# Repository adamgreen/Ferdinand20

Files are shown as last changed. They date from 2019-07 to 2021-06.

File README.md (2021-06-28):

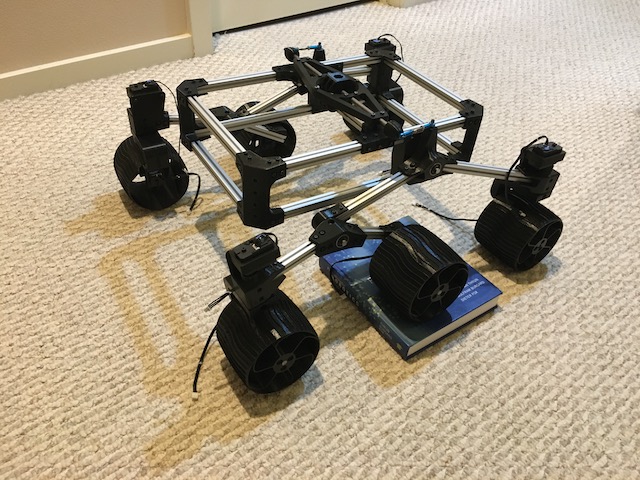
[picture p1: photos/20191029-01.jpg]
Sawppy Rover
<br>
Tracking the build of my robot to compete in the
[Seattle Robotics Society's Robo-Magellan](https://robothon.org/rules-robo-magellan/) competition that was to be held on October 3rd, 2020 at the Seattle Center but is now cancelled due to COVID-19. Development of this robot will continue in hopes that it can compete in the future.

## Points of Interest
[SRS Robo-Magellan rules](https://robothon.org/rules-robo-magellan/) <br>
[Notes about our 2014 bot](https://github.com/adamgreen/Ferdinand14#readme) <br>
[Notes from my stalled 2016 attempt](https://github.com/adamgreen/Ferdinand16#readme) <br>
[How to Clone GitHub Repository](#clone-this-repo-and-its-submodules) <br>
[Sawppy the Rover Build Instructions](https://github.com/Roger-random/Sawppy_Rover#readme) <br>

---
## June 27th, 2021
### I2C? What I2C?
The next task I set myself upon was wiring the IMU into the LPC1768 on my Sawppy bot so that I could use it with the [dead reckoning code that I wrote for the Ferdinand16 project](https://github.com/adamgreen/Ferdinand16/tree/master/firmware/robot). When I was working with the IMU hardware back in April, I had it connected to a dedicated LPC1768 on a breadboard and not the one already wired up to my bot. When I went to move it over to the LPC1768 microcontroller on the Sawppy bot, I hit a snag. All of the I2C capable pins on the microcontroller were already being used for their UART functionality: LX-16A servos/motors, MRI debug monitor, and PDB communication.

### Bridge It
In the future, I plan to create my own PCB for the LPC1768 based brains of my bot which will give me access to more pins of the microcontroller. In the meantime, I would like to continue prototyping with the mbed based board that I already have. How can I work around the lack of free I2C pins? It turns out that I still have one set of SPI pins available. Using another microcontroller, I could create a bridge device that reads the IMU sensors via I2C and then sends the resulting readings to my main microcontroller over SPI.

#### LPC1768 as SPI Slave
My first attempt at building this bridge was to use another mbed LPC1768 microcontroller as a SPI slave. When I originally skimmed the mbed SPISlave class documentation I was kind of confused on how to really use it. I then read the LPC1768 User Manual and was even more confused. I tried for several days to get the LPC1768 to reliably send data back to the SPI master but ended up throwing in the towel. I just don't think the SPI peripheral on the LPC1768 hardware is designed properly for use in slave mode:
* There is no way to get an interrupt when the master sends a single byte request. It will only interrupt when the Rx buffer overflows, the Rx FIFO is half full, or 4 byte times have elapsed since the last received byte.
* It is really hard to queue up the Tx data at the right time and if you don't have it queued in time because your code is busy doing something else, the peripheral just takes the oldest already sent data from the Tx buffer and sends it instead.

In the end, I gave up on the LPC1768 and decided to research using another microcontroller from my stash.

#### nRF5x as SPI Slave
I had an [Adafruit Feather nRF52 Pro with myNewt Bootloader - nRF52832](https://www.adafruit.com/product/3574) in my stash of development boards so I pulled up its SPI slave documentation. What I saw there looked very promising:
* You can specify what data should be returned when you have no active data queued up to be sent back.
* Once you do have data to be sent, you queue it all up at once with the help of EasyDMA.

I ported my I2C sensor reading code to the nRF52832 and quickly implemented the SPI bridging code. The SPI Slave functionality on this device worked exactly as expected and I soon had a functional bridge setup between the bot's main LPC1768 and the nRF52 bridge.

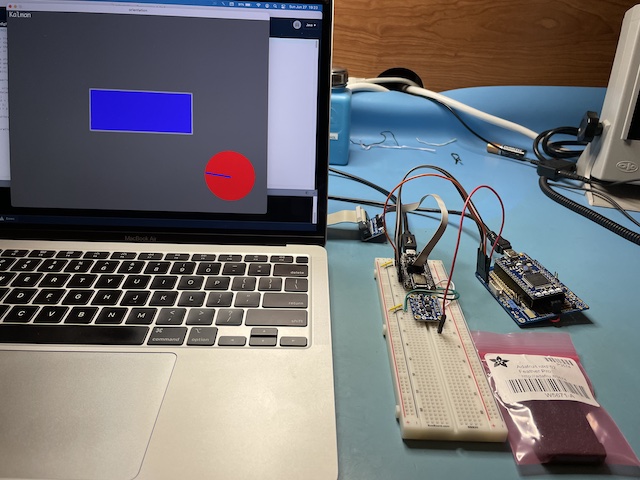
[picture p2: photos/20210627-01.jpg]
nRF52 bridge connected to LPC1768


Now to get it all installed back on my bot and start writing some dead reckoning code :)

---
## June 4th, 2021
### LX-16A Encoders
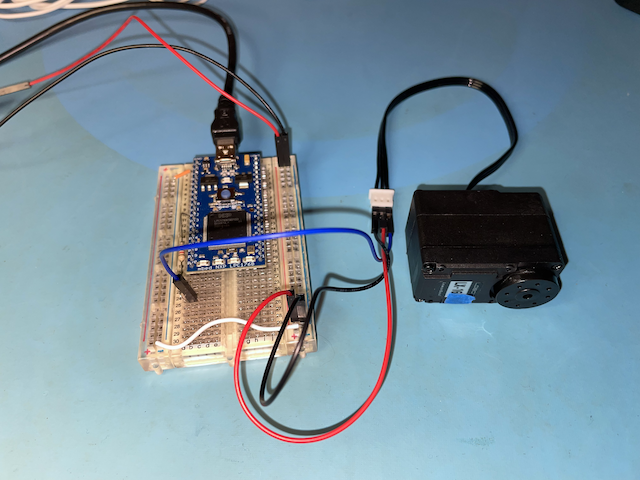
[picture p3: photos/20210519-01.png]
LX-16A Test Setup
 <br>

The [LX-16A servos](https://www.hiwonder.hk/collections/servo/products/hiwonder-lx-16a-serial-bus-servo) used in the [Sawppy Rover](https://github.com/Roger-random/Sawppy_Rover#readme) design have a potentiometer that can be used for reading out the current angle but it can't accurately read all 360 degrees of the rotation. It returns accurate readings between -40 and 280 degrees (320 degrees of rotation) but not such accurate readings for the other 40 degrees of rotation. There are 2 types of inaccurate readings that it returns when in the range between 280 and -40 degrees (the deadzone):
* It will return angle values that fall between 280 and -40 as expected but they aren't accurate. This is the most common case and is easy for me to detect in code. I suspect that there is a carbon arc for the section where it returns correct values (-40 to 280 degrees) and maybe just copper at the two extremes where it returns these incorrect readings. The following diagrams show what I think the internals of the potentiometer look like and where the wiper is located for a few key angles:
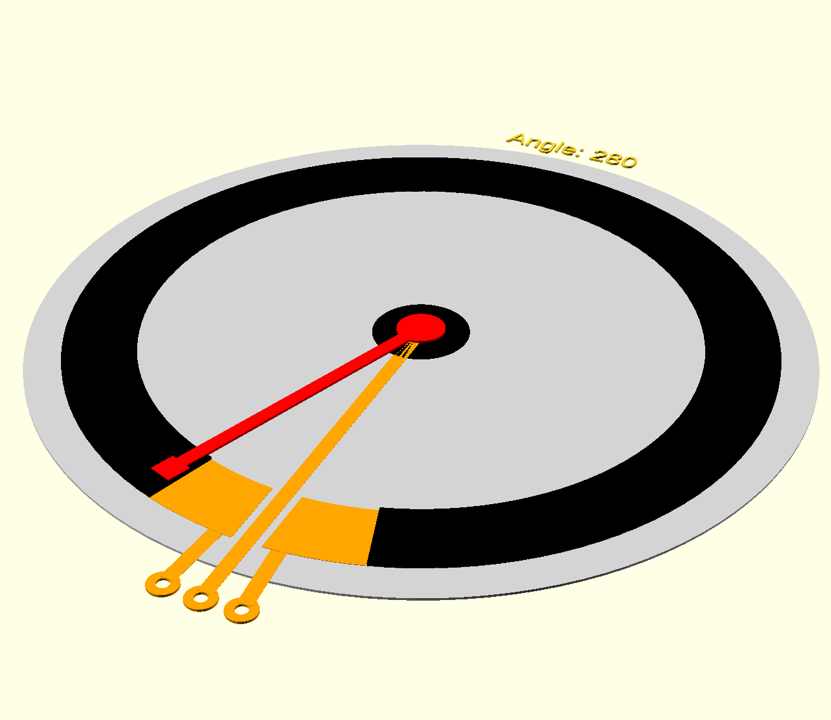
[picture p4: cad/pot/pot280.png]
Angle at 280 degrees
  * 280 degrees: This is the maximum valid angle. The potentiometer wiper is contacting the carbon resistive track. <br>
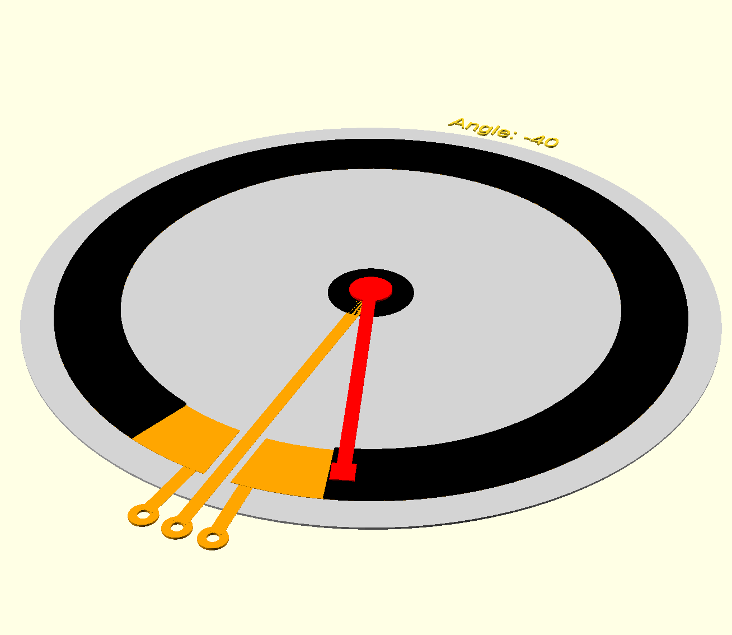
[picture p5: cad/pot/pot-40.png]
Angle at -40 degrees
  * -40 degrees: This is the minimum valid angle and shows the potentiometer wiper at the other end of the carbon resistive track. <br> 
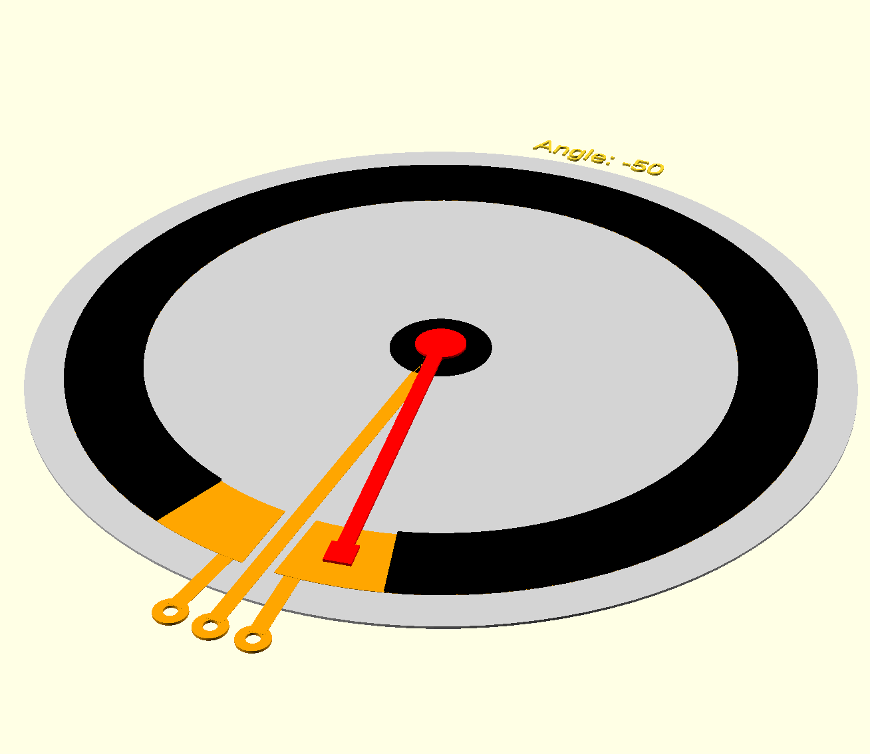
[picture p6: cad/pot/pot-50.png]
Angle at -50 degrees
  * -50 degrees: This is an angle in the deadzone. The potentiometer is no longer on the carbon resistive track but is also not floating. This explains why the readings back from the LX-16A servo tend to fall around -40 or 280 when in the deadzone since this area of the track is at either the maximum or minimum voltage level since there is so little resistance to the end taps. <br> 
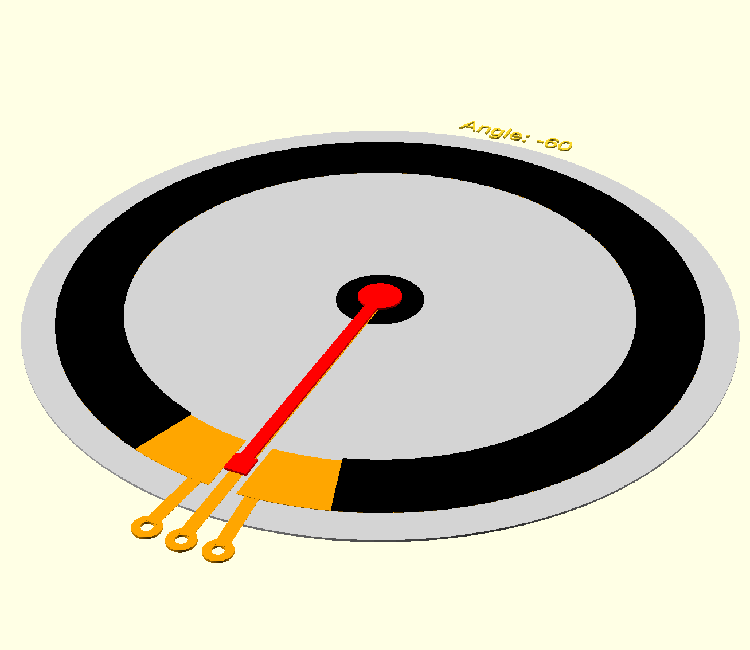
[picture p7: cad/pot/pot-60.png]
Angle at -60 degrees
* It will return random angle readings that can fall anywhere in the 360 degree range. I suspect that this happens when the potentiometer wiper is left floating in a gap that must exist between the two ends of the potentiometer to stop the wiper from creating a short between the high and low voltages applied to the opposite ends of the potentiometer. This isn't a common case and is hard to detect in code but we do know that it happens when previous readings place it in the deadzone and the wiper shouldn't dwell in this area for long at the velocities and sampling times that will be used for controlling my robot's motion. <br> 

I tried two methods to work around these inaccurate readings and I will give an overview of them below.

#### Kalman Approach
Kalman Filter Book <br>
As the old saying goes, "When all you have is a hammer, everything looks like a nail." In my case, my hammer of choice has become the Kalman filter. So my first thought to solve the LX-16A servo encoder problem was to apply a Kalman filter to calculate the current rotational position and velocity. To this end, I started out by re-reading my ["Kalman Filter for Beginners with MATLAB Examples" by Phil Kim](https://www.amazon.com/Kalman-Filter-Beginners-MATLAB-Examples/dp/1463648359). I really like this book. The content is very good. The only down point is the Korean to English translation could use quite a bit of improvement. Once I finished the reread, I wrote up some code to experiment with the Kalman filter which can be seen in the following [commit](https://github.com/adamgreen/Ferdinand20/commit/b95c3b9d9873d6a039cecfaa98e94790804dd103). I played with this code for a few days but I never got the error estimates to a point where the rotational velocity estimate wasn't overly filtered with a lagging response to real world velocity changes. Based on these results, I decided to try another approach which can be best described as a bunch of conditional hacks.

#### Conditional Hacks
The key observation that I take advantage of in my set of hacks is the following:
* If the angle returned from the LX-16A servo is between -40 and 280 degrees, then most likely it is within +/-0.24 degrees (1 lsb) of the actual real world position.

This means that my code treats such position measurements as the truth and uses them to estimate the velocity. There is one exception to this and I will discuss it more later.

The second observation is very much related to that first one:
* If the angle returned from the LX-16A servo is instead between 280 degrees and -40 degrees then it is in a deadzone where the returned values are much less accurate.

When my code detects that the returned position readings are in this deadzone, it uses the previous position and velocity estimates and sampling time to calculate new position estimates by assuming constant velocity between the samples.

The handling of those two angle ranges gets us most of the way to a solution but I needed to add a few more conditional hacks to produce a functional filter:
* When the wiper is in the middle of the deadzone, it will be floating and returning completely random values that fall in or outside of the deadzone. I have the code ignore the first non-deadzone sample when the previous sample was from the deadzone. If this ignored non-deadzone angle is followed by another then the code transitions into the non-deadzone logic previously described. This does mean that the first good angle reading is always dropped when transitioning out of the deadzone but that is a small price to pay for filtering out these completely erroneous readings. I only expect a single erroneous reading caused by a floating wiper when the rover is moving since there should be a very low likelihood that the wiper stays in this region for multiple samples as the motor is rotating.
* Don't update the velocity until it has two or more non-deadzone position readings. The last interpolated position from the deadzone logic might be so incorrect that it would result in a very bad estimate of the velocity.
* Use an exponential recursive moving average filter to smooth out the velocity calculations. We don't want high frequency noise in this calculation to later impact the PID control loop.

```c++
void LX16A_DriveMotor::updateState()
{
    // Calculate time since last running of the filter and grab the current servo position in close temporal
    // relation to the time capture.
    int16_t servoPos = m_servo.getPosition();
    uint32_t currSampleTime = m_timer.read_us();
    uint32_t elapsedMicroSec = currSampleTime - m_lastSampleTime;
    m_lastSampleTime = currSampleTime;
    float dt = (float)elapsedMicroSec / 1000000.0f;

    EncoderState prevState = m_currState;
    if (ignoringNonDeadZoneSamples(servoPos) || isServoInDeadZone(servoPos))
    {
        // The servo position could be off by as much as +/-20 degrees when in dead zone of the pot.
        // Assume that the motor is still spinning at the same rate when in dead zone.
        m_currState.angle = constrainAngle(prevState.angle + prevState.velocity * dt);
        m_currState.velocity = prevState.velocity;
        m_wasInDeadZone = true;
        printf("*");
    }
    else
    {
        // The pot reading should be accurate so use it.
        m_currState.angle = constrainAngle(servoPos * LX16A_SERVO_TO_RADIAN_VALUE);

        if (m_wasInDeadZone)
        {
            // Don't want to base current velocity off of previously interpolated position.
            m_currState.velocity = prevState.velocity;
        }
        else
        {
            // Calculate velocity from change in angle and then use weighted average so that it doesn't snap too much.
            const float weight = VELOCITY_AVERAGING_WEIGHT;
            float angleDelta = constrainAngle(fmodf(m_currState.angle - prevState.angle, 2.0f*(float)M_PI));
            float velocity = angleDelta / dt;
            m_currState.velocity = (1.0f-weight)*m_currState.velocity + weight*velocity;
        }
        m_wasInDeadZone = false;
    }

    updatePID(dt);
}
```

I may have to add code in the future to handle the motor being stopped when in the deadzone or even worse, stopped right at the point where the potentiometer wiper is left floating. I will cross this bridge once I encounter it so that I have scenarios to use for testing my attempts to resolve it.

### Closing the Loop
Once I had a way to obtain a reasonably reliable estimate of the servo's rotational velocity, I pulled over my PID code from my old [Ferdinand16 repository](https://github.com/adamgreen/Ferdinand16#readme). The biggest changes I made to this code after copying include:
* Now allowing the sample time to be changed between PID updates as the frequency of the LX-16A servo position reads may not be as consistent as my previous uses of the PID control algorithm.
* Ferdinand16 required the angle error to be normalized between +/- 180 degrees and the PID code had this hardcoded into it. I updated the code to take an optional callback for performing such normalizations when required. It isn't required for LX-16A motor velocity control.

Now that I had a way to close the loop on the control of the motor velocities, I went into the existing ```SawppyDrive``` class and plugged in my new ```LX16A_DriveMotor``` class for controlling the 6 servos that spin the wheels (while leaving the 4 turning servos as is). Once this switch had been made, I could drive my Sawppy bot around by remote control as before but now the wheel velocities were running under closed loop control.

### MRIPROG / BLEMRI Issues with new macOS and MRI Updates
When I started testing the new PID code on my actual Sawppy based robot, I hit a few issues with my Bluetooth Low Energy (BLE) programming/debugging tools that I had to address first. It turns out that it needed updates to work with the newer version of my [MRI debug monitor](https://github.com/adamgreen/mri#readme), my new MacBook Air, and Big Sur updates:
* I updated **mriprog** to move the entry point for the LPC1768 bootloader into entry.S so that I can use assembly language code to initialize the stack pointers (MSP & PSP) to the desired value since the current MRI doesn't allow for modifying the stack pointers from GDB. Once the stack pointers are set, it just branches to the original main() code.
* MRI now contains 6 more special registers in the context (MSP, PSP, PRIMASK, BASEPRI, FAULTMASK, CONTROL). I updated **mriprog**'s gdbRemote module to take these into account.
* When my new laptop communicates with the nRF51 BLE to UART bridge, it tends to corrupt a few packets that need to be resent. I made a few updates to **mriprog** to better handle these resends:
  * Instead of reporting each packet error encountered, just count them and report the number of retries at the end along with the other statistics.
  * Reduce PACKET_MAX_DATA from 16k to 4k so that if the CRC fails on a packet then less data needs to be resent.
* I updated my **blemri** code to handle a BLE change introduced with Big Sur. Once the Mac has been connected to a BLE device such as BLEMRI, Big Sur only returns the information that it cached on the first connection and this doesn't include the 128-bit service UUID from the scan response. My code used this UUID for filtering when performing BLE device discovery. I modified the firmware to no longer advertise the unique service UUID and now just advertise the Nordic UART service UUID actually supported by the device as it is no longer of use for filtering. I now have the application running on macOS perform BLE discovery with no filtering and then check the local device name on each discovered device, looking for ones named BLEMRI.
* I increased the minimum and maximum connection interval from 7.5ms to 15ms in my BLEMRI firmware to meet the Apple design recommendations. My iPhone is now able to stay connected for over 100 seconds. My iPhone would previously drop the connection when it couldn't agree with the device on connection parameters. This change doesn't decrease the throughput that much as BLE allows multiple packets to be scheduled per interval. It would increase the turn around time to get the response back from commands. The throughput is still above 5kB/s after this change so I will keep it.
* I copied the **mriprog** utility from my [older BB-8 project](https://github.com/adamgreen/bb-8/tree/master/mriprog) and placed it in its [own repository](https://github.com/adamgreen/mriprog) so that it could be included as a submodule in this Ferdinand20 repository.

### Next Steps
* ~~Debug and fix some of the issues that I encountered while performing the latest testing on my Sawppy control code.~~
* Wire the IMU into the LPC1768 on my Sawppy bot.
* Port my [heading maintaining code from my Ferdinand16 project](https://github.com/adamgreen/Ferdinand16/tree/master/firmware/robot) and get it working on this bot.

---
## April 23rd, 2021
### New IMU Hardware - Up and Running!
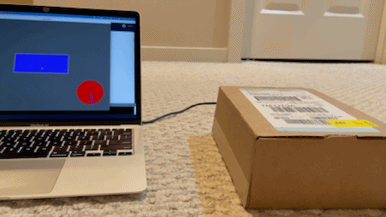
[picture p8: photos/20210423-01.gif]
Animated GIF of IMU
<br>
I spent this week getting the [Adafruit Precision NXP 9-DoF Breakout Board](https://www.adafruit.com/product/3463) working with my existing [Ferdinand16](https://github.com/adamgreen/Ferdinand16#readme) IMU code:
* I copied over the Kalman filter and I2C drivers and got them working in a newer build environment:
  * I updated my FlashFileSystem driver to work with the newer build of the mbed SDK. This file system is used to read the ```config.ini``` embedded in the firmware image as part of the build process.
  * I reorganized the code to move the drivers out into a ```libs/``` folder so that they didn't clutter up the ```software/``` folder.
* I rewrote the I2C drivers to work with the NXP FXOS8700CQ Accelerometer/Magnetometer and the NXP FXAS21002C Gyroscope:
  * My original IMU code only ran at 100Hz. I added the ability to switch between sampling rates (100/200/400Hz) from a setting in ```files/config.ini```. I am now using 200Hz for testing as 400Hz swamps the UART with too much data when communicating the orientation back to the PC in certain scenarios. It could probably run at 400Hz on the robot though as it doesn't require this communication.
  * Now samples the FXOS8700CQ Accelerometer/Magnetometer measurements on a data ready interrupt rather than a fixed timer. According to an errata from NXP, this is supposed to decrease the chance of I2C communications interfering with the magnetometer analog front end.
* I copied over my [Ferdinand14 calibration application](https://github.com/adamgreen/Ferdinand14/tree/master/calibration) and it pretty much just worked with the latest release of Processing.
* I was then able to use the calibration application to [calculate the settings for these sensors](https://github.com/adamgreen/Ferdinand14#august-19-2014) and update them in ```files/config.ini```.
* I copied over my [Ferdinand16 orientation application](https://github.com/adamgreen/Ferdinand16/tree/master/processing/orientation) and got it working on newer builds of [Processing](https://processing.org):
  * I had to use the Processing 4 alpha as the 3D graphics are broken in the current Processing 3 release on macOS.
  * I fixed some bugs that I noticed when testing my new sensor that I must have missed in previous testing 5 years ago.
  * I updated it to pull more configuration options from the ```config.ini``` rather than being hardcoded (variance settings, sampling rate, etc) in the sources. It also now reads from the same ```files/config.ini``` built into the firmware so that they use matching configuration options.
  * This program is used to measure the gyro and accelerometer/magnetometer variances to be placed in ```config.ini```. If the sensor is left unmoved for a few minutes, the statistics of how each sensor contributes to noise in the quaternion representation of the orientation will be dumped to the Processing console.

Issues I encountered while testing this port:
* The temperature readings on the NXP FXAS21002C Gyroscope  are lower resolution than the InvenSense ITG-3200 Gyroscope that I used before. This limits the resolution of the gyro drift compensation that I can use on this sensor. The good news is that this gyro shows significantly less drift during my testing at temperatures between 20 and 30C.
* While the gyro drift was pretty low when the die temperature was between 20 and 30C, it showed some very odd non-linear drift characteristics at lower temperatures which would be difficult to calibrate away. Luckily my bot isn't likely to be running at lower temperatures and the drift appears to be linear above 20C so my existing drift compensation can still be used to further reduce the drift.
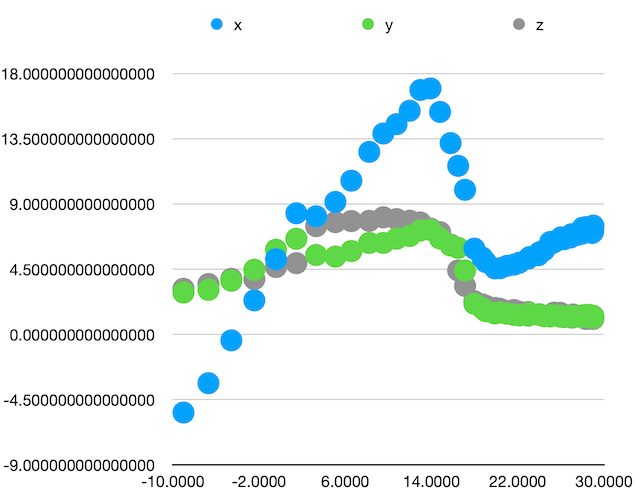
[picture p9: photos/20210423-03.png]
Drift vs Temperature Graph

* The NXP FXAS21002C Gyroscope measurements contain more noise than I encountered with the InvenSense ITG-3200 Gyroscope. The noise resulted in a 10x increase in the ```compass.gyro.variance``` setting.
```diff
-compass.initial.variance=1.0E-4
-compass.gyro.variance=6.5E-11
-compass.accelerometer.magnetometer.variance=1.0E-5
+compass.initial.variance=2.0E-4
+compass.gyro.variance=6.0E-10
+compass.accelerometer.magnetometer.variance=2.0E-4
```
* I see a lot more jitter in the orientation when run in Accelerometer/Magnetometer only mode. This jitter can also be seen in the Kalman filtered results, though much reduced as one would expect. If I hardcode the magnetometer reading and only use the accelerometer, there is almost no jitter at all so it is the magnetometer that causes it. Actually I think the accelerometer in the NXP FXOS8700CQ is better than the one I used previously.

### What's Inside the Box?
What's inside the brown box shown in the animated GIF at the beginning of this post?
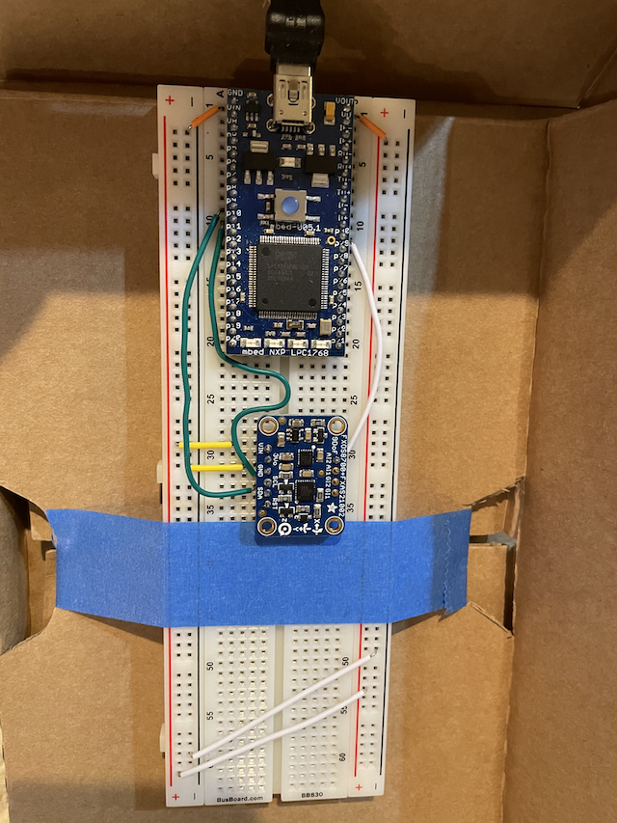
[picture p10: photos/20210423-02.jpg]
Inside the Box
<br><br>
It contains a [mbed 1768](https://os.mbed.com/platforms/mbed-LPC1768/) connected to a [Adafruit Precision NXP 9-DOF Breakout Board](https://www.adafruit.com/product/3463).

### Next Steps
Now that I have my IMU code working again on newer hardware, I want to continue fleshing out the dead reckoning part of the project. With that in mind, I will concentrate on the following next week:
* ~~Determine distance travelled by the wheels on my [Sawppy](https://github.com/Roger-random/Sawppy_Rover#readme) frame.~~

---
## April 16th, 2021
### Upgrade my IMU Hardware?
#### Sparkfun 9 DoF - Sensor Stick
Sparkfun 9 DoF - Sensor Stick</br>
Back in 2014, I decided to use the [Sparkfun 9 DoF - Sensor Stick](https://www.sparkfun.com/products/retired/10724) as the accelerometer, magnetometer, and gyroscope for our [Ferdinand14 project](https://github.com/adamgreen/Ferdinand14#readme).

#### Adafruit Precision NXP 9-DOF Breakout Board
Adafruit Precision NXP 9-DOF Breakout Board</br>
When starting out on Ferdinand20, I noticed that Sparkfun no longer sells this board. This was a good reason to look around at new sensors as I suspected there would now be even more precise units on the market. This research led me to the [Adafruit Precision NXP 9-DOF Breakout Board](https://www.adafruit.com/product/3463) which appears to offer more precision in all axis. I ordered one of these new IMU boards from Adafruit back in July of 2019. This way I would have it if I decided to make the leap and update my Kalman filter to work with a more current sensor package. I spent time this week evaluating whether I should make that leap:
* I code reviewed my existing [Kalman filter and I2C drivers](https://github.com/adamgreen/Ferdinand16/tree/master/libs/Sparkfun9DoFSensorStick). From looking at this code, it seems that the only work that would need to be completed to make the switch would be updating the I2C drivers to work with the newer NXP sensors, run a calibration pass, and update the config.ini with the new calibration data. Nothing else was specific to the sensors in use.
* I read the datasheets for the NXP FXOS8700CQ Accelerometer/Magnetometer and the NXP FXAS21002C Gyroscope to learn how difficult it would be to update the I2C drivers. From what I read in those datasheets, it should only take a part of a day to make those updates. They are pretty simple and the FXOS8700CQ datasheet even includes sample C code. I also noticed that these sensors look like they all have more precision than my current IMU hardware and can run at a higher sample rate (400Hz vs 100Hz). The only thing less precise is the temperature readings on the gyroscope which might have an impact on my drift corrections.

### Next Steps
Based on my recent research, I think it should only take a week or two to switch to this new IMU hardware:
* ~~I need to update the I2C drivers for the two chips on this new breakout board.~~
* ~~Run the resulting raw sensor readings through my [existing calibration process](https://github.com/adamgreen/Ferdinand14#august-19-2014) to create an updated config.ini.~~
* ~~Test the new hardware with my [existing Processing based GUI](https://github.com/adamgreen/Ferdinand16/tree/master/processing/orientation).~~

---
## April 11th, 2021
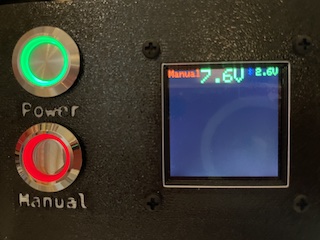
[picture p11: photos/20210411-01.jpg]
New Manual Switch


Last year I updated the Power Distribution Board enclosure to use a round push button switch for the Manual/Auto mode selection but I only had a green version of the switch on hand. I now have a [red version of the switch](https://www.adafruit.com/product/916) that I could install instead.

---
## April 9th, 2021
### BLE Remote Experiments
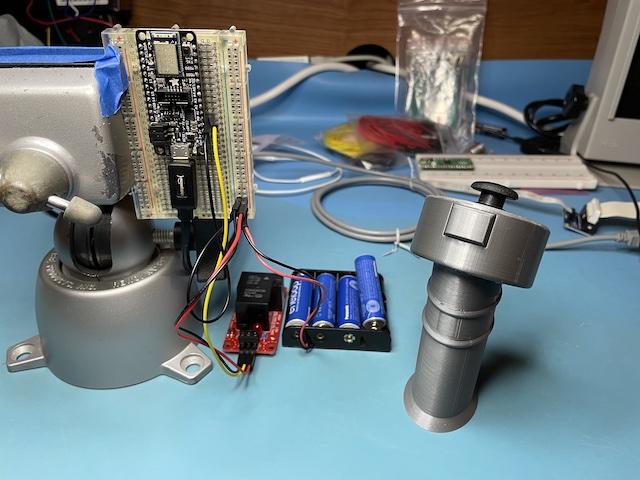
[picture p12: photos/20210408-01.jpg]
BLE Experiment


The BLE connection between the power distribution board (PDB) and the remote control that I built last year isn't as reliable as my initial prototypes. I conducted a few experiments this week to help narrow down what might be the cause. These experiments included:
* Running my PDB code on a micro:bit again like I did in the initial prototype. This did seem to work a bit better than the PDB hardware in my actual robot but not significantly better. I think the fact that I didn't initially have the logic to shutoff the relay after missing ```MAX_MISSED_BLE_PACKETS``` packets from the remote is the main reason I didn't see the problem on the earlier prototype.
* I tried moving the relay in relation to the BLE antenna. It didn't seem to have a noticeable impact. I could even place the relay right over the antenna and it didn't become any less reliable.
* If I placed a low resistance load across the relay outputs to allow a largish current (~5A) to flow, that seemed to cause more problems for the BLE connection. Especially if placed too close to the antenna.
* I tried switching to an [Adafruit Feather nRF52 Bluefruit LE - nRF52832](https://www.adafruit.com/product/3406) with its chip antenna. It actually performed worse than the micro:bit setup with its PCB antenna.
* I found that holding the remote control so that its PCB was in the vertical orientation resulted in some of the best increases in reliability, even with the PDB mounted in the actual robot.

### Lessons Learned:
* Keep high current traces on PDB away from the BLE antenna.
* Have antenna on BLE modules protruding out over the PCB if possible.
* Mount BLE PCB antenna in vertical orientation.
* For PDB, place it at top so there isn't much between it and the remote control.
* For remote, try to place it so that my hand won't be between the two antenna.

---
## March 29th, 2021
### Cone Detection?
The computer vision unit of the [RoboGrok course](http://www.robogrok.com) showed a way to highlight red objects by subtracting the green and blue channel values from the red channel value so that only pixels with red and no blue and/or green component would show up brighter. The following two screen captures show what a traffic cone and a Robothon 2015 t-shirt look like when viewed with this red-only pixel filter applied. The left window in each screen capture shows the full RGB of the scene and the right window shows the same scene with the red-only filter applied.
#### Normal Indoor Lighting
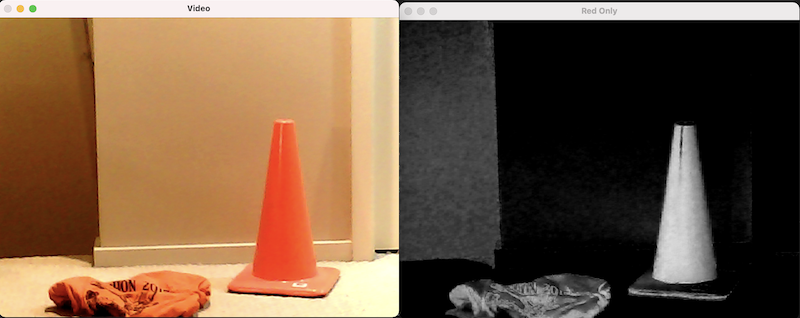
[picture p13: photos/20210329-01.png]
ScreenCapture of cone in normal light

#### Reduced Indoor Lighting
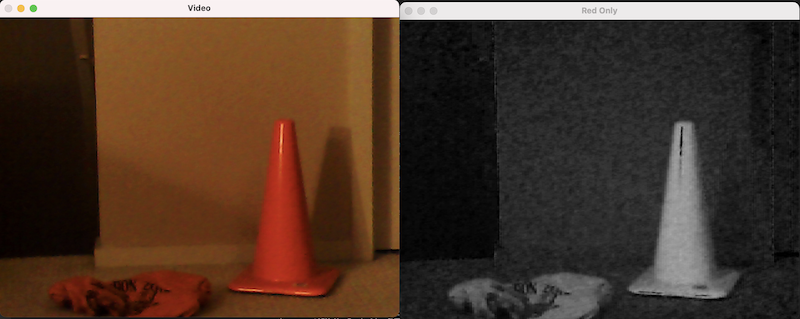
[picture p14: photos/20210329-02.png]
ScreenCapture of cone in less light


Some key takeaways from this experiment:
* In both lighting situations, the traffic cone always shows up as one of the brightest things in the red-only image. When testing inside, I never really got any false negatives where the cone wouldn't show up as one of the brightest objects in the red-only image.
* There are false positives, as we can see that the orange Robothon t-shirt shows up quite bright as well.
* Running connected components on the red-only image could segment the image into separate bright red/orange objects like the traffic cone and t-shirt.
* Additional object recognition algorithms would need to be run on each of the segmented objects to remove the false positives and only identify the traffic cones of interest.
* During previous outdoor testing I noticed that traffic cones show up as bright white when all color channels are saturated by the bright sunlight. I need to perform more outdoor testing to see if I need to add a physical filter such as [this one](https://openmv.io/collections/products/products/polarizing-filter).

### Future Computer Vision Work
I have decided not to continue with this experimentation on my MacBook Air any further as I plan to use the [OpenMV camera](https://openmv.io) on the actual robot and it makes more sense to continue future experimentation with that device instead.

When I get back to looking at cone detection, I should probably first address these work items:
* Code review the OpenMV code base and see how it is implemented incase I want to modify some of the low level C/C++ code instead of just using the Python layer.
* Can I attach the OpenMV camera to my robot, drive it around, and record video footage? This would be useful for future playback and testing while I develop/refine the cone detection algorithm.
* Do some internet searching to see if anyone else has already come up with a robust cone detector using the OpenMV camera.

---
## March 23rd, 2021
### Starting Back Up
I paused this project for a few months to get some work done on other projects:
* [Halloween foam pumpkin with dragon eyes](https://github.com/adamgreen/DragonEyes).
* Updated my [NeoPixel Christmas tree](https://github.com/adamgreen/NeoPixelTree) to use a more robust 3D printed frame with a pre-made string of lights.
* Learned more about OpenSCAD by designing a few things that I needed around the house.
* I completed the [RoboGrok online robotics courses](http://www.robogrok.com), Robotics 1 and Robotics 2. While some of the material in the course is applicable to mobile robots like this one, it concentrated more on industrial type of applications (ie. robotic arms).

### Next Steps
* ~~The [RoboGrok course](http://www.robogrok.com) had some interesting sections on computer vision. I would like to take some of my vision coursework and try modifying it to detect traffic cones for the [Robo-Magellan](https://robothon.org/rules-robo-magellan/) competition.~~
* ~~The BLE connection between the power distribution board and the remote control that I built for the bot last year isn't as reliable as my initial prototypes. I want to do some experiments to determine what the actual cause is so that I can redesign it in the future.~~
* ~~Figure out how I want to progress on the IMU front by picking one of the following approaches:~~
  * ~~Hack up a connection to the IMU that I built for my earlier [Ferdinand16](https://github.com/adamgreen/Ferdinand16) attempt.~~
  * ~~Port the Ferdinand16 firmware to work with the [NXP 9-DoF Breakout Board - FXOS8700 + FXAS21002](https://www.adafruit.com/product/3463) IMU board that I bought from Adafruit when I started working on Ferdinand20.~~

---
## October 19th, 2020
### Project on Pause
If the 2020 running of the SRS Robo-Magellan competition hadn't been cancelled this year, it would have been run a couple of weekends ago. I wouldn't have had enough ready to actually compete this year though. I haven't even started on the main robot control electronics yet. Before I finalize the PDB design and start working on those main control electronics, I want to take a break and work on some other foolish electronic projects. Hopefully I can get back to this project before the end of the year and get it ready for next year's competition.

---
## September 27th, 2020
I have completed the updates to the PDB enclosure to make it smaller and look less out of place on the back of the Sawppy rover.

### Old PDB Enclosure
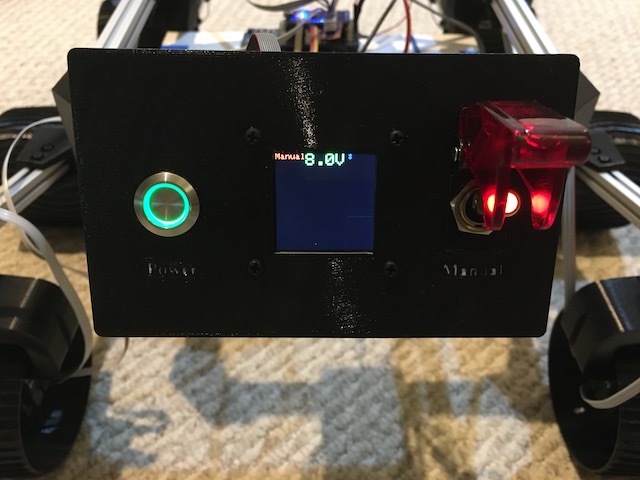
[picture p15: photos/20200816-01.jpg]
Photo of old PDB Installed #1

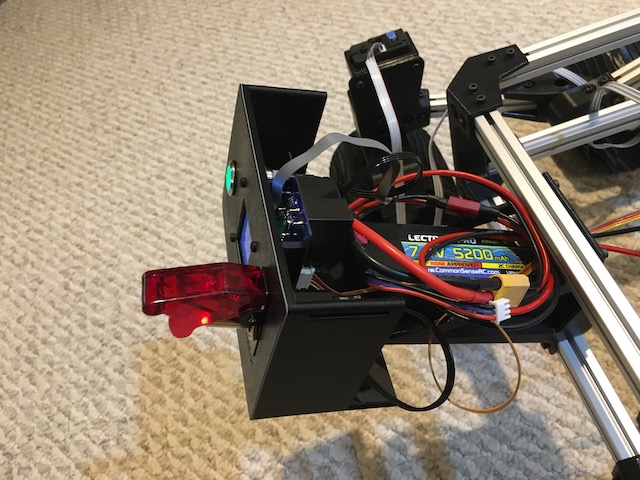
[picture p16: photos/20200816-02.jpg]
Photo of old PDB Installed #2


### New PDB Enclosure
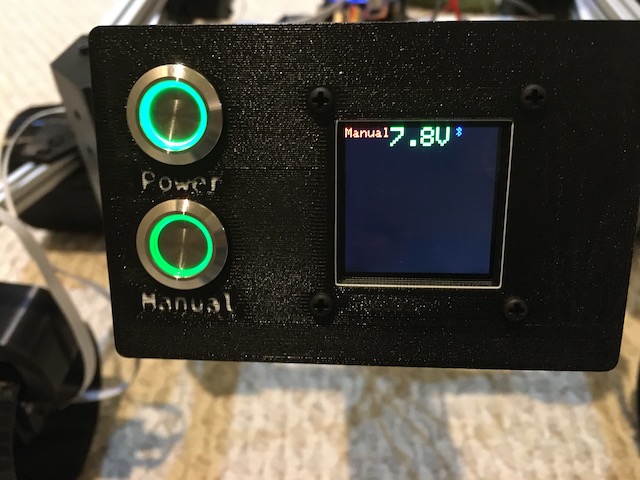
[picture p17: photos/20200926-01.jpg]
Photo of new PDB Installed #1

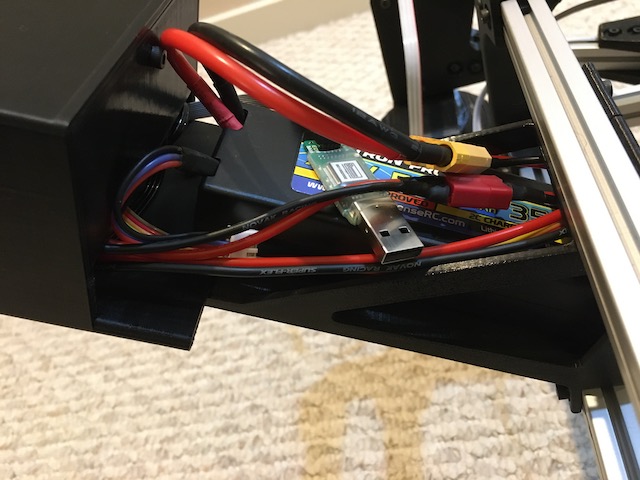
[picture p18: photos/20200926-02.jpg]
Photo of new PDB Installed #2


I made it smaller by dropping the large covered toggle switch for the manual/auto mode selection and instead used the same model as the power switch. I am currently using a green lit one since that is what I had on hand but I will probably purchase a red one and use it in the future instead. I also rotated the PCB by 90° which helped reduce the height of the enclosure. The OpenSCAD design was modified to take the dimensions of the PCB, switches, and label text to automatically calculate the smallest possible enclosure size.

Once I had the size reduced, I added a top and removable back panel to hide the internal electronics and make it a bit more tolerant of wet outdoor conditions.

---
## September 14th, 2020
I completed the first functional prototype of the remote control enclosure last weekend.

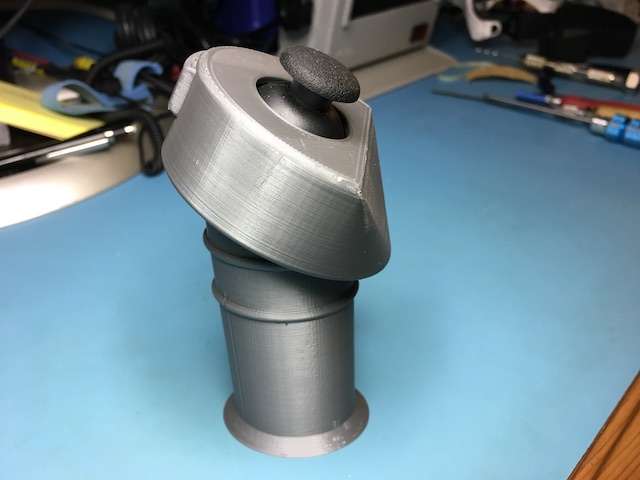
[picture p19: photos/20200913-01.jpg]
1st Functional Remote Prototype


I still have tweaking that I want to do on its 3D design. Before I do that though, I will probably switch back to the 3D design of the Power Distribution Board Panel and apply some tweaks that I have been thinking about since I mounted the last one on my bot.

---
## August 27th, 2020
I am still cranking away at OpenSCAD, working on the enclosure for the remote control. I have been iterating on the design of the button used to depress the deadman switch so I have just been printing that portion of the remote control top to speed things up:<br>
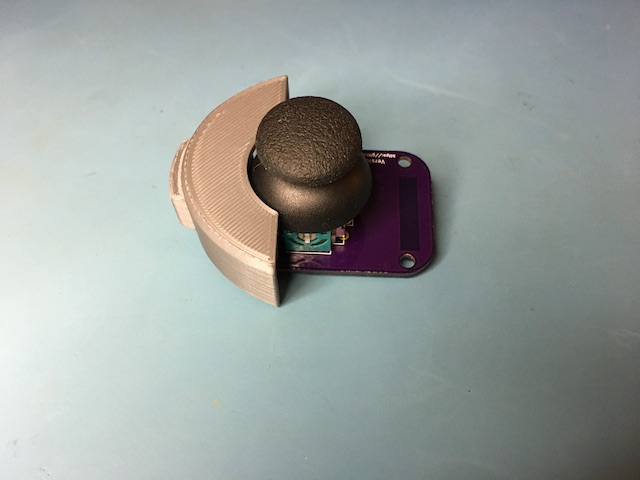
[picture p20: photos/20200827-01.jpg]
Test print of remote control from top

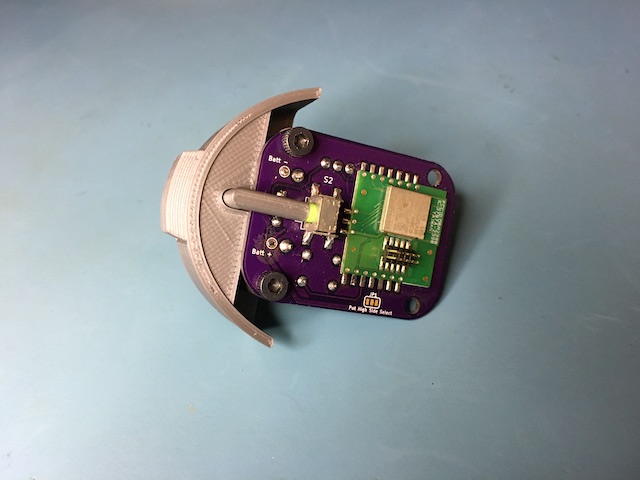
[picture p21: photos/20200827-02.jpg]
Test print of remote control from bottom


I will be taking a break from this project for a few days while I work on another project. Once I am done with that, I will start working on the handle for the remote control.

---
## August 21st, 2020
I have been busy with OpenSCAD this week, trying to turn my previous remote control mockup into a functional enclosure. I still have quite a bit more work to do before I complete it but I thought I would share some photos of my current progress:<br>
* I designed a mockup of the PCB with joystick installed to digitally place in the enclosure and check for fit.<br>
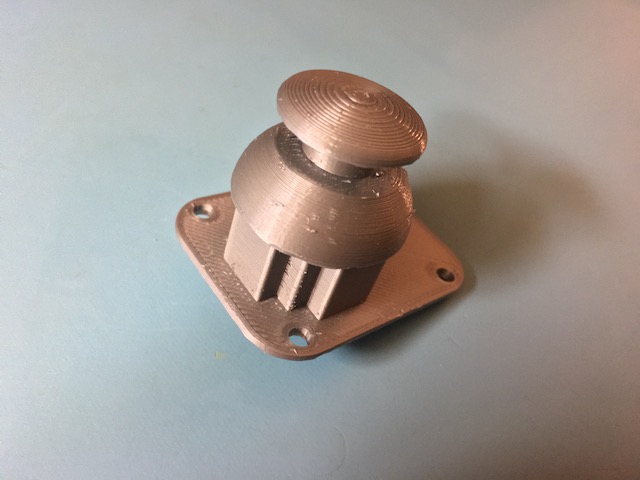
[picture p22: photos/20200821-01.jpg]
Photo of 3D printed representation of PCB/Joystick

* I now have everything in the top portion of the remote control completed except for the button to activate the deadman switch.<br>
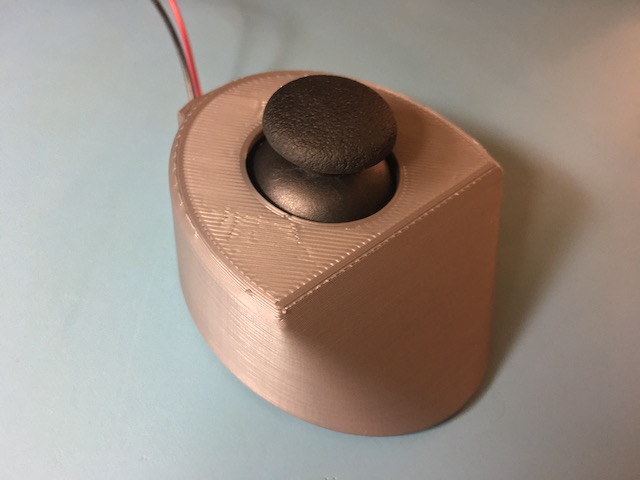
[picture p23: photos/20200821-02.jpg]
Test print of remote control top from top

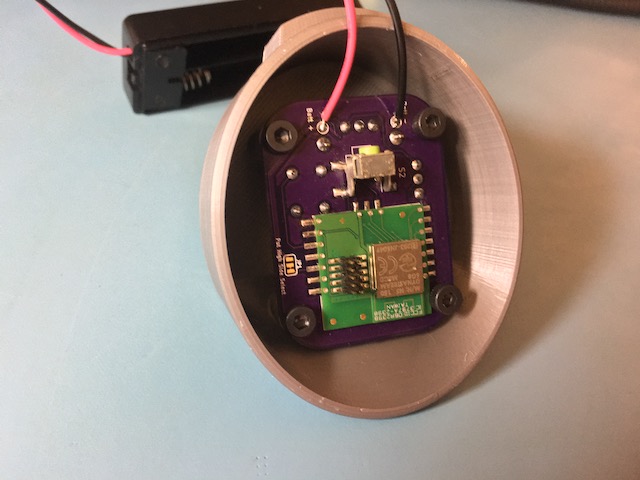
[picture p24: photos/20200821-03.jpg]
Test print of remote control top from bottom


---
## August 16th, 2020
### 3D Printed PDB Panel
Photo of PDB Installed #1
Photo of PDB Installed #2

This weekend I finished the OpenSCAD design for the PDB enclosure and got it mounted on the Sawppy frame. It works but there are some things I might improve in the future:
* It is a little larger than I would like. It doesn't really fit in with the scale of the Sawppy rover itself.
* The switch labels are a bit hard to read. I should use a more legible (fatter & simpler) font. Switching to one layer of white filament for the layer that bridges behind the text does make it pop though so I will continue to do that in the future.
* Tilt the screen up to make it easier to view when standing behind it.

I demoed my rover at today's online [Vancouver Robotics Club meetup](https://www.meetup.com/VancouverRoboticsClub). It was nice to have made enough progress on it to have something that I could actually demo.

### SRS Robothon 2020 Cancelled
Donna Smith was at today's meetup and announced that [Robothon will be cancelled for 2020](https://robothon.org/2020/05/18/announcing-robothon-20202/). I now have another year to get this rover ready for competition.

### Next Steps
* ~~Start working on the OpenSCAD design of the enclosure for the remote control based on my existing prototype.~~

---
## August 12th, 2020
### PDB Installed - Kind Of
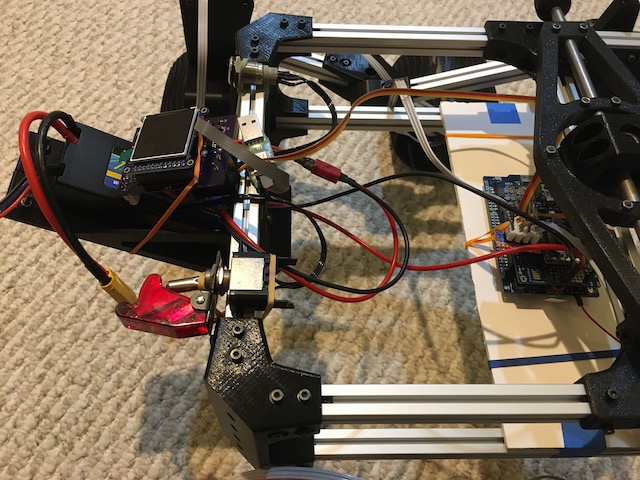
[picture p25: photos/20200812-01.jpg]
PDB Hacked onto Sawppy
<br>
Since I haven't designed the panel for the PDB yet, I used elastic bands to mount the PDB to the Sawppy frame for now. Hacky but it worked! Once the PDB was temporarily mounted I was able to update the SawwpyDrive test code to make use of the PdbSerial driver to drive the rover around using the remote control.

When I first started using the remote control with Sawppy I noticed that the motor power relay would click on and off as I moved around the robot. I ended up increasing the **MAX_MISSED_BLE_PACKETS** define in the PDB firmware to allow up to 30 missed packets before flagging the remote as disconnected.

### Next Steps
* ~~Start working on the OpenSCAD design of the panel to be mounted on Sawppy to contain the PDB electronics.~~

---
## August 11th, 2020
### Feature Complete
I now consider the firmware for the [Power Distribution Board](software/PDB) and [Remote Control](software/RemoteControl) units to be feature complete. I have also implemented the [PdbSerial driver](software/PdbSerial) to make it easier for the robot microcontroller to interact with the PDB. The inbound auto/manual packets from the PDB are processed in the UART ISR as the bytes arrive and the outbound informational text to the PDB are sent in the background using DMA.

### Next Steps
* ~~Connect the motor power outputs from the PDB to the LPC1768 robot microcontroller board.~~
* ~~Write code for the LPC1768 to let it be driven around via the remote control when the PDB is in manual driving mode.~~
* ~~Start working on the OpenSCAD design of the panel to be mounted on Sawppy to contain the PDB electronics.~~

---
## August 9th, 2020
### Remote Control PCBs
The remote control PCBs arrived from OSHPark earlier this month.
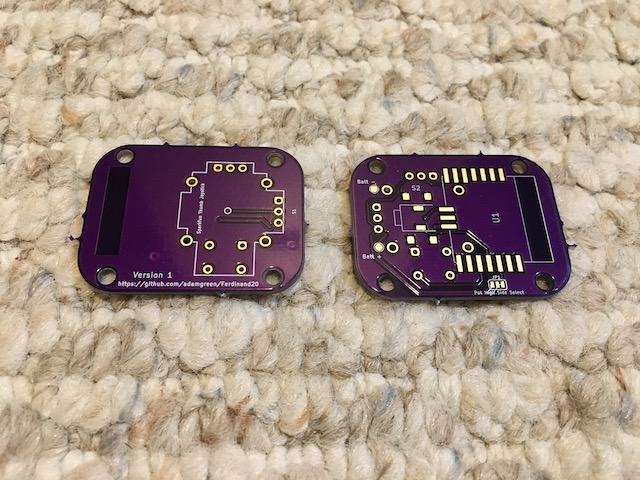
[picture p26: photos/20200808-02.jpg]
Remote Control Bare PCBs
<br><br>
A day after the boards arrived, I soldered them up.
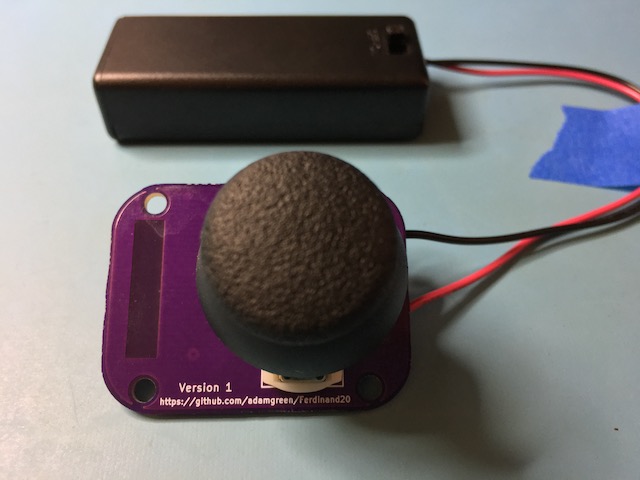
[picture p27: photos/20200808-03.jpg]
Remote Control Soldered PCB Top
<br>
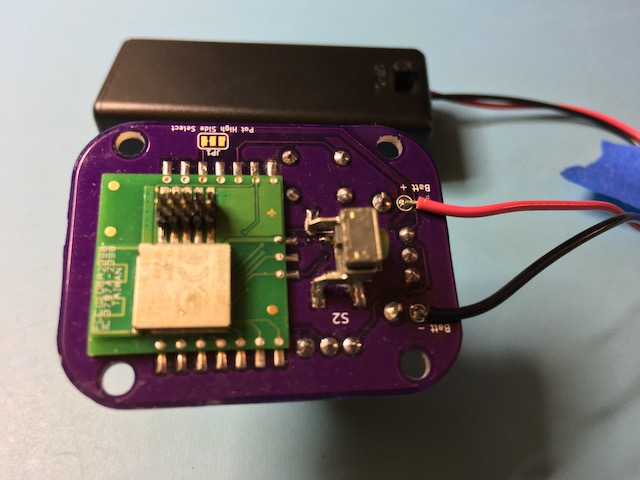
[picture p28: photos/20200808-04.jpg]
Remote Control Soldered PCB Bottom
<br><br>
There are only a few things I would change if I were to respin this board:
* The ground pads didn't have enough thermal relief. The ground plane was pretty large on this board and it really wicked a lot of heat away from the soldering iron.
* The pads on the right angled dead man switch should have been longer to make it easier to make contact with the soldering iron.

Once I had the PCBs soldered up, I updated the firmware to work on them and then got to quickly finalizing the code.

### Remote Control Current Usage
With the remote control code finalized I was to start measuring the remote's current usage in various states:
| BLE State | Current |
|---|---|
| Fast Advertising | 2mA |
| Normal Advertising | 1.1mA |
| Connected & Sending JoyData | 1.5mA |
| Deep Sleep | 20µA |

The 2xAAA batteries should be able to power the device in deep sleep for quite some time. That means that I don't need to use a power switch on the remote control. I already have it coded to enter deep sleep after 4 minutes of not being connected to the PDB and pressing the dead man switch will wake it up so that it can attempt to reconnect to the PDB.

### Power Distribution Board - More Firmware Improvements
The following photos show the top and bottom of the PDB PCB after I applied bodge wires to work around the mistakes that I made in the original PCB design:
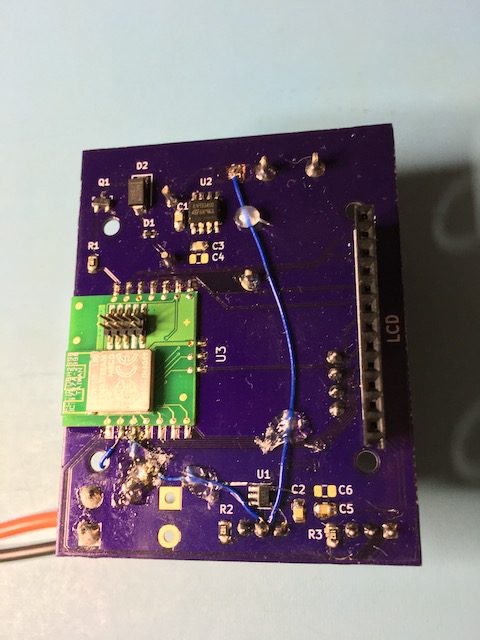
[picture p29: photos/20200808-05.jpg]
PDB Top
<br><br>
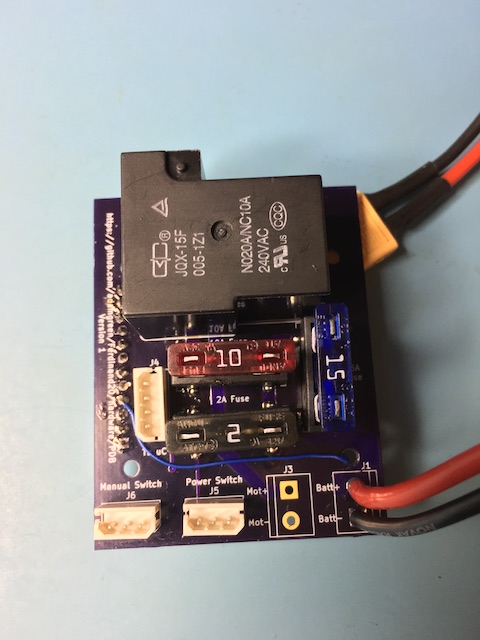
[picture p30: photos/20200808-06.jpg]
PDB Bottom
<br>

Over the last week, I have continued to work on the PDB to improve its firmware:
* I added a serial connection between the PDB and the LPC1768 based robot microcontroller. This included code which can send the latest PDB and remote control status to the robot microcontroller and accept informational text sent from the robot to display on the LCD.
* I improved the performance of the ST7789 LCD driver by porting @cbm80amiga's [Arduino_ST7789_Fast](https://github.com/cbm80amiga/Arduino_ST7789_Fast) library and then tweaked it to get the best performance in my nRF51422 setup.

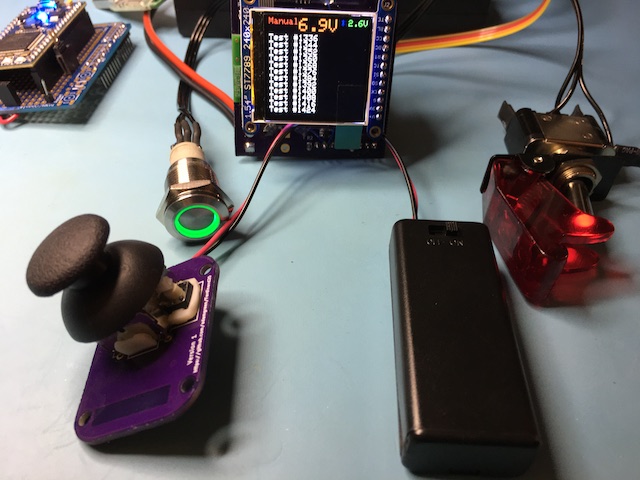
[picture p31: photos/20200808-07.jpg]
Complete PDB Setup
<br>

---
## July 31st, 2020
### Power Distribution Board - Firmware Updates
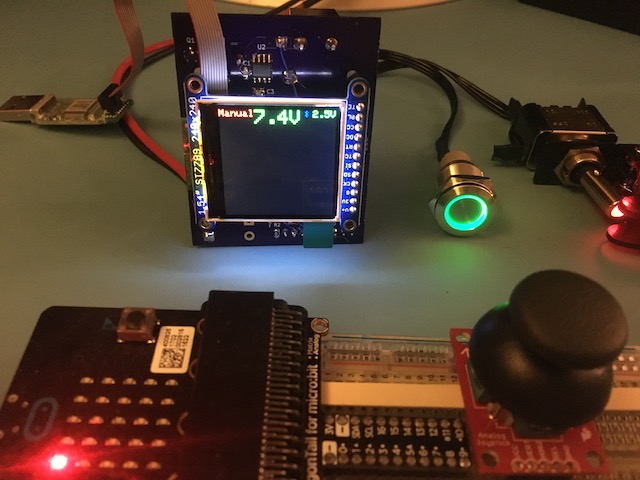
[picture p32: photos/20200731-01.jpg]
Photo of latest PDB firmware running


I have made some pretty major updates to the PDB firmware and now have it reporting most of the robot power state:
* Manual/Auto mode switch setting.
* Connection state of the BLE based remote control.
* Current battery voltage of the robot's main 2S LiPo battery.
* Current battery voltage of the battery in the remote control.
* A motor icon will be lit up on the display when the dead man switch is pressed on the remote control, enabling the motor power on the PDB.

I did apply a few bodge wires to version 1 of the PDB:
* The 5V regulator's input power is now switched on and off with the main power switch, just like the 3.3V regulator. Previously it was always getting power as long as the battery was plugged in.
* I moved the LCD_SCK from pin P0.6 to P0.12, feeing up an ADC pin for reading the LiPo battery voltage.
* I now connect the switched LiPo battery voltage to P0.6 (AIN7) via a 330/680 ohm voltage divider to reduce the >7V LiPo voltage to something safe for nRF51 pins and comparable to the built-in 1.2V VBG reference.

My first attempt at routing the LiPo battery voltage to P0.6 ended up with me doing some major damage to my nRF51 module and shorting the 3.3V power rail to ground. This happened because I forgot to route the LiPo battery voltage through a voltage divider before applying it to the nRF51 ADC pin. I had to remove that nRF51 module and replace it with a new one. The second time, I remembered to use the voltage divider.

The major features still missing from the PDB are related to UART handling and I will start working on them next:
* When in manual mode, it needs to send the joystick status to the main robot microcontroller.
* It also needs to accept informational text from the main microcontroller and display it on the LCD.

### Remote Control - PCBs on their Way
I received an email from OSHPark yesterday indicating that the PCBs for the remote control electronics have been fabricated and are on their way to me in the mail. They should arrive in a day or two. Once they arrive, I will switch away from the PDB electronics temporarily and solder up the remote control electronics and test it out to see if there is anything I need to revise in that design.

---
## July 25th, 2020
### Power Distribution Board Version 1 - Ready for Action
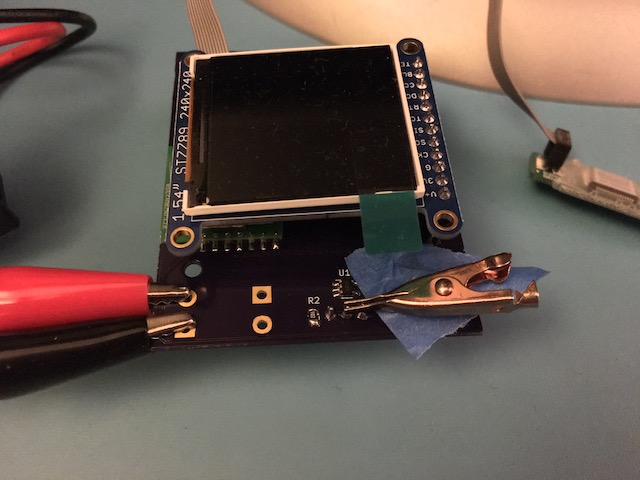
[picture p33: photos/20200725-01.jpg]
Initial PDB Testing


This week I soldered the parts down to version 1 of the PDB PCB and got the existing firmware up and running on it. The voltage regulators (3.3V and 5V) both work as expected, the LCD works as well, the NRF51 module is able to connect with my remote control prototype, and pressing the deadman switch on the remote control successfully energizes the relay for enabling motor power.

### Power Distribution Board Improvements
As I was soldering up the board and testing it, there were a few things I noticed that I would change if I ever update the PCB design:
* Just use one 2.2uF capacitor on the outputs of the regulators instead of the two 1uF that I currently have in the design. These are what the regulator datasheets recommend but I didn't have any here when I designed the boards but I do now.
* The 0805 footprints I used for the capacitors and resistors were very hard to hand solder. The pad is completely covered by the part, making it difficult for me to get the iron on both the pad and the component to properly heat them. KiCAD has hand soldering friendly footprints in its library so I would like to try them next time.
* The D1 footprint I used is way too small for hand soldering. There are SOD123 variants of this chip available from Digikey which are larger and the footprint for it is also in their KiCAD library.
* The F2 and F3 fuse holders are so close together that it is hard to solder the last one in. F3 could have been moved a bit lower.
* I am not switching the 5V supply with the main power switch. It is currently always getting power. I will rework the current board to correct this issue.
* I need to connect an ADC capable pin on the nRF51 module to the battery voltage so that it can report the battery voltage to the user on the LCD. I will rework the current board to correct this issue.

### Next Steps
* ~~Finalize the PDB firmware. It is easier to work on the PDB firmware while the electronics are on the desk since it makes the SWD debugging port more accessible.~~
* ~~Start working on the OpenSCAD design of the panel to be mounted on Sawppy to contain the PDB electronics.~~

---
## July 21st, 2020
The Power Distribution Board PCBs arrived from OSHPark yesterday. I will soon start soldering them up. These are the first custom PCBs that I have had made for this project so it is pretty exciting.<br>
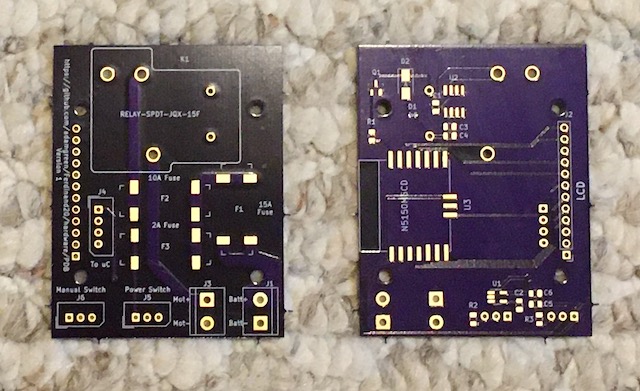
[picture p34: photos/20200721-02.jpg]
PDB PCBs from OSHPark


---
## July 20th, 2020
The Power Distribution Board PCB left [OSHPark](https://oshpark.com) at the end of last week and should arrive at my home today. While waiting for that board to be fabricated, I have been working on the KiCAD design for the BLE based Remote Control which wirelessly connects to the PDB.

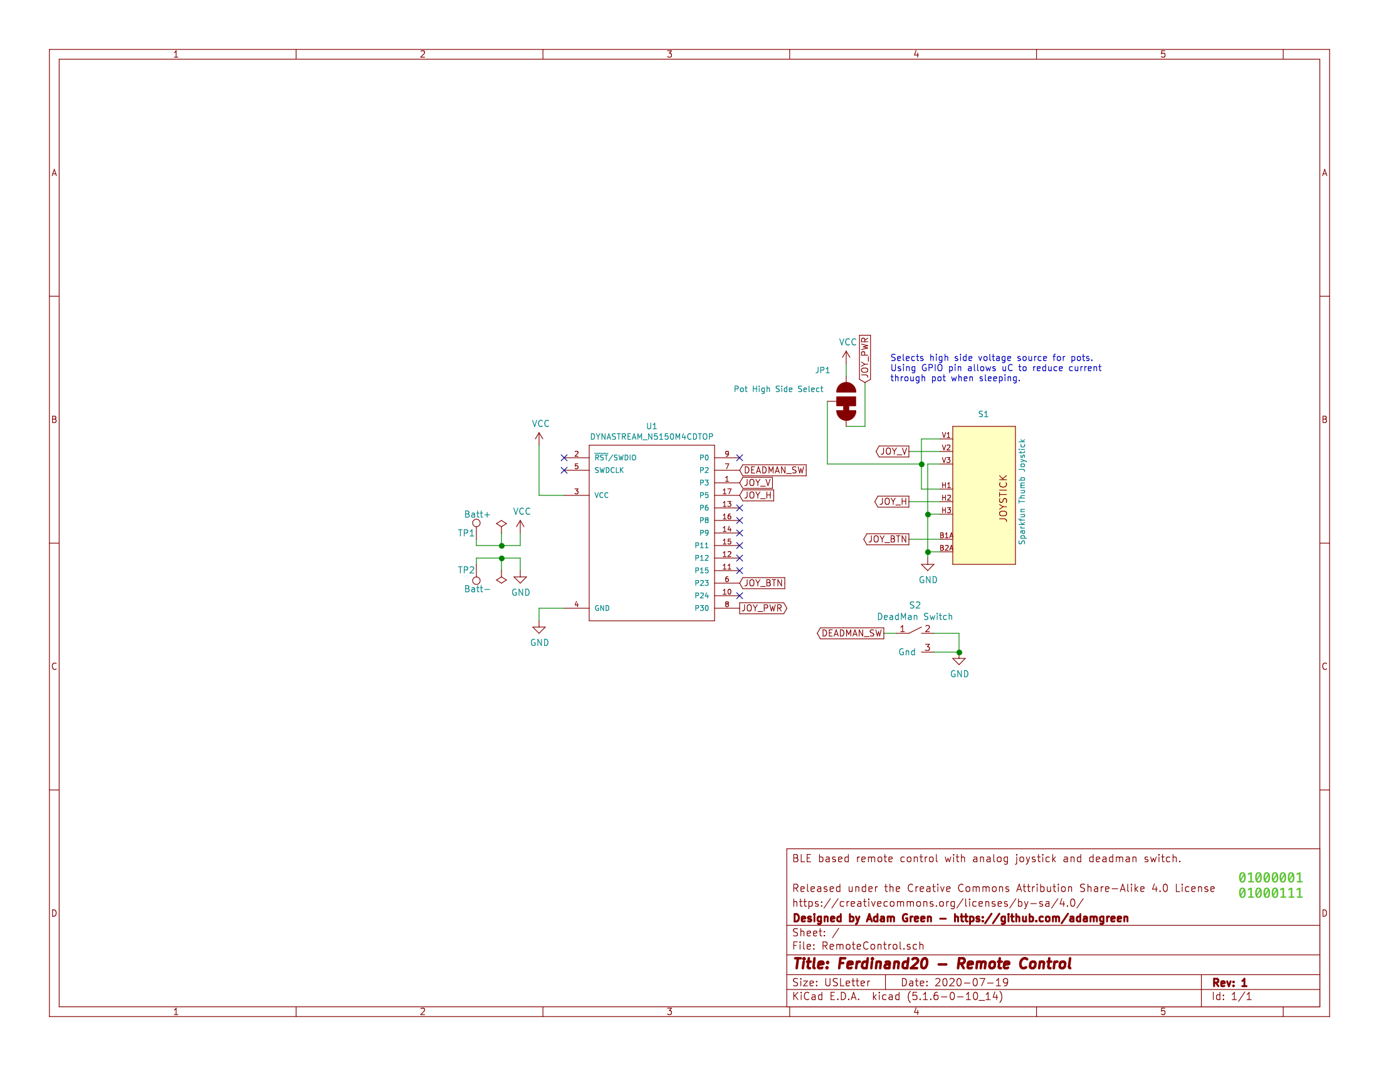
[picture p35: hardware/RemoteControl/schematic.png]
Remote Control Schematic
<br>
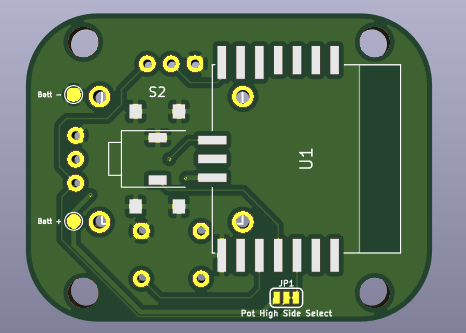
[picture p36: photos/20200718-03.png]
Remote Control PCB


I sent the above Remote Control PCB design off to OSHPark for fabrication this morning.

I also worked on a nonfunctional [OpenSCAD](https://www.openscad.org) mockup for the remote control at the same time as I worked on the PCB layout so that I could make sure that the PCB would fit within the model. It also let me check whether things like mounting holes, switches, thumb stick, etc need to be moved. I broke the mockup design down into two pieces:
* The top which will contain the thumb stick, deadman switch, and electronics.<br>
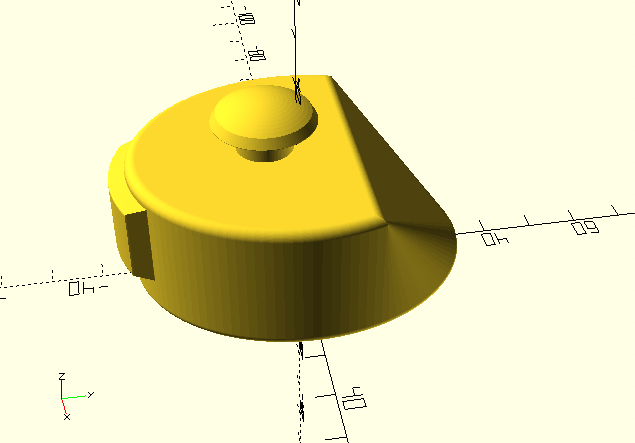
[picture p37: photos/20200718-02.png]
Remote Control Top

* The handle which will contain the 2xAAA battery pack.<br>
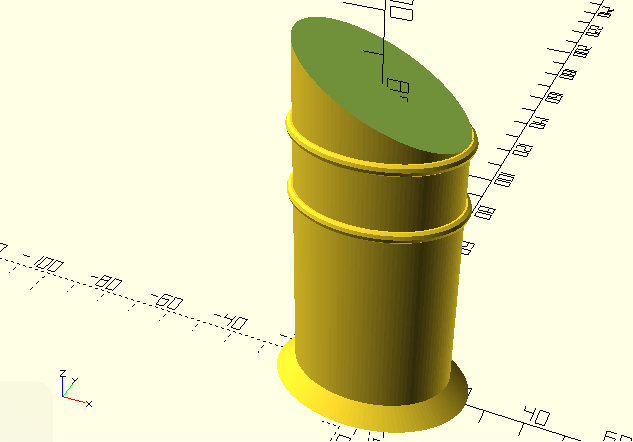
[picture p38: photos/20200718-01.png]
Remote Control Bottom


Here is what it looked like after I 3D printed those two parts and glued them together:<br>
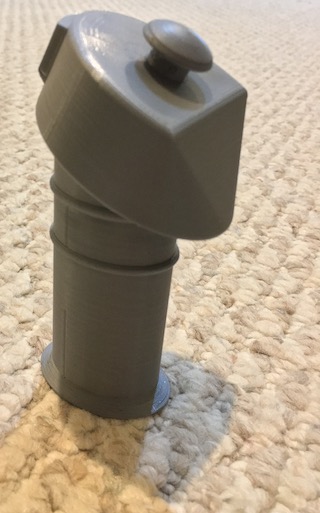
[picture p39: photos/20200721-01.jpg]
Photo of 3D printed remote control mockup


Now that the PDB PCB is scheduled to arrive today, I will concentrate on that part of the project for the next couple of weeks:
* Soldering and testing the PDB.
* Start working on the OpenSCAD design of the panel to be mounted on Sawppy to contain the PDB electronics.

---
## July 6th, 2020
I have now learned enough KiCAD to complete version 1 of the Power Distribution Board, PDB, for my Robo-Magellan bot.
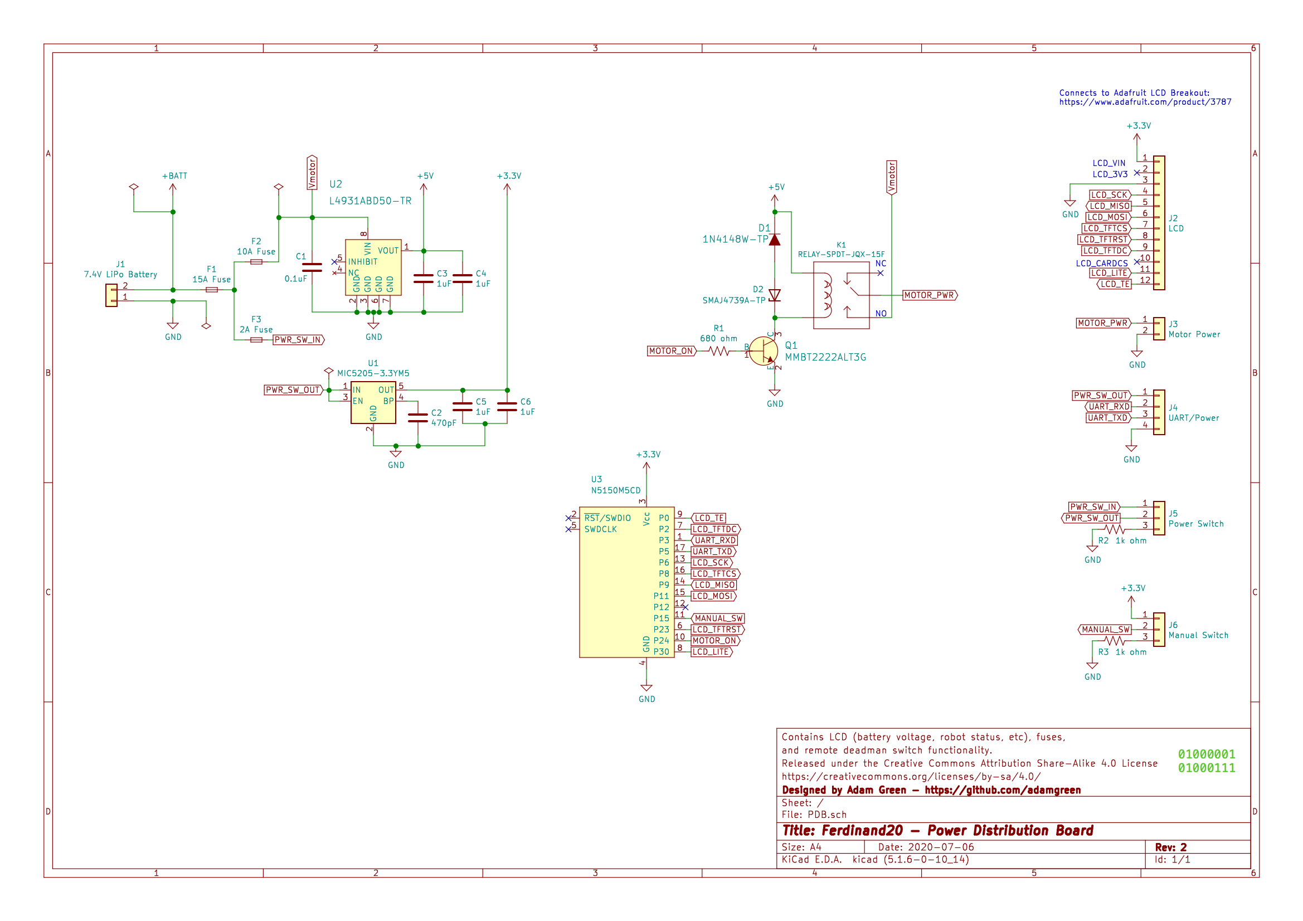
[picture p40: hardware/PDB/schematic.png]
PDB Schematic
<br>

I have uploaded the resulting KiCAD layout to [OSHPark](https://oshpark.com) and am now just waiting for them to be manufactured. I used their [2oz copper service](https://docs.oshpark.com/services/two-layer-hhdc/) to allow for narrower traces to handle the maximum 10A motor current.
<br>PDB PCB Front
PDB PCB Back

### Next Steps
* ~~Design a PCB for the BLE based remote control electronics.~~
* ~~Solder up the PDB once the PCB arrives from OSHPark.~~

---
## May 30th, 2020
Digikey parts

### Amazon & Digikey Orders Have Arrived
The parts that I ordered earlier this week from Amazon and Digikey have already arrived and the order from Sparkfun shipped today. I now have all of the parts for which I would want to validate footprints so it is definitely time to get cracking on that PCB design for the Power Distribution Board.

---
## May 28th, 2020
I decided to order the parts for the Power Distribution Board before I even start the design so that I can verify footprints as I am new to KiCAD and even more likely than usual to mess up some footprints. To facilitate that verification, I have completed my initial swag at a BOM and ordered up the parts from [Amazon](https://www.amazon.com), [Sparkfun](https://www.sparkfun.com), and [Digikey](https://www.digikey.com).

### Amazon Order
* [Blade Fuse Assortment Kit](https://www.amazon.com/dp/B077RXSWVH) - This assortment includes the 2A (digital electronics switched by main power switch and not relay), 10A (motor power switched by relay), and 15A (maximum overall battery current) valued fuses that I currently plan to use for protecting this project.

### Sparkfun Order
* [Metal Pushbutton - Latching (16mm, Green)](https://www.sparkfun.com/products/11973) - Use as the main power switch.
* [Toggle Switch and Cover - Illuminated (Red)](https://www.sparkfun.com/products/11310) - Use to enable the manual driving mode. This type of switch makes it hard to put it into manual driving mode by mistake and makes it easy for judges and me to see if it is running in manual driving mode.
* [Thumb Joystick](https://www.sparkfun.com/products/9032) - This is the same thumb joystick that I am using in my current breadboard prototype of the remote control.
* [Tactile Button - SMD (6mm)](https://www.sparkfun.com/products/12992) - Use for dead man switch on the remote control.
* [XT60 Connectors - Male/Female Pair](https://www.sparkfun.com/products/10474) - Use to connect the 2S LiPo battery to the Power Distribution Board.

### Digikey Order
* 3 x [Fuse Holder 20A 1 Circuit Blade Surface Mount](https://www.digikey.com/product-detail/en/3587TR/36-3587CT-ND) - Use to hold the 3 blade fuses I plan to use on the Power Distribution Board. These are surface mount versions.
* 3 x [Fuse Block 30A 500V 1 Circuit Blade Through Hole](https://www.digikey.com/product-detail/en/3557-2/36-3557-2-ND) - These are through hole versions of the above blade fuses holders. I ordered both to see which I prefer for this project.
* 1 x [Linear Voltage Regulator IC 1 Output 150mA SOT-23-5](https://www.digikey.com/product-detail/en/MIC5205-3.3YM5-TR/576-1259-1-ND) - Use on the PDB to provide 3.3V to the nRF51 and TFT display from the 2S LiPo battery. I measured the current being used by the existing prototype to see how much the micro:bit and TFT LCD use together and it was about 60mA. The final electronics will probably be a bit lower as the micro:bit has an extra USB interface chip which won't be included in the final project. The 150mA provided by this regulator should be more than enough for the 3.3V electronics on the PDB itself.
* 1 x [Linear Voltage Regulator IC 1 Output 250mA 8-SO](https://www.digikey.com/product-detail/en/L4931ABD50-TR/497-1156-1-ND) - Use on the PDB to provide 5V for the relay coil. The coil needs around 150mA so this 250mA regulator should be sufficient.
* 1 x [Bipolar (BJT) Transistor NPN 40V 600mA 300MHz 300mW Surface Mount SOT-23-3 (TO-236)](https://www.digikey.com/product-detail/en/MMBT2222ALT3G/MMBT2222ALT3GOSCT-ND) - This switches the 5V to the relay coil based on the state of a nRF51 GPIO pin.
* 1 x [Zener Diode 9.1V 1W ±5% Surface Mount DO-214AC (SMA)](https://www.digikey.com/product-detail/en/SMAJ4739A-TP/SMAJ4739A-TPCT-ND) - Part of the relay coil support circuitry on the PDB.
* 1 x [Diode Standard 75V 200mA Surface Mount SOD-523F](https://www.digikey.com/product-detail/en/1N4148WT/1N4148WTCT-ND) - Part of the relay coil support circuitry on the PDB.
* 1 x [DEANS CONNECTOR - M/F PAIR](https://www.digikey.com/product-detail/en/PRT-11864/1568-1659-ND) - Use to connect the PDB to the motors.
* 30 x [Socket Contact Tin 22-28 AWG Crimp](https://www.digikey.com/product-detail/en/0039000160/WM9661CT-ND) - I purchased more crimp pins than I need for the below connectors to make sure that I have plenty of spares.
* 2 x [Connector Header Through Hole 3 position 0.098" (2.50mm)](https://www.digikey.com/product-detail/en/0022035035/900-0022035035-ND) - These will be used to connect the two panel mounted switches (power and manual override) to the PDB.
* 2 x [3 Rectangular Connectors - Housings Receptacle  0.098" (2.50mm)](https://www.digikey.com/product-detail/en/0050375033/WM18874-ND)
* 2 x [Connector Header Through Hole 4 position 0.098" (2.50mm)](https://www.digikey.com/product-detail/en/0022035045/WM18888-ND) - These will be used to connect power and UART signals lines from the PDB to the main microcontroller.
* 2 x [4 Rectangular Connectors - Housings Receptacle  0.098" (2.50mm)](https://www.digikey.com/product-detail/en/0050375043/WM17405-ND)
* 2 x [Bluetooth Bluetooth v4.1 Transceiver Module 2.4GHz Integrated, Trace Surface Mount](https://www.digikey.com/product-detail/en/N5150M5CD/1094-1021-ND) - I have used these nRF51422 based modules in the past. Both the PDB and the remote control will need one of these.

---
## May 24th, 2020
It feels good to get back into this bot building project and crossing off two work items this week.

Photo of ST7789 Display and Relay
### ST7789 LCD Driver Port
I completed the port of [Adafruit's ST77xx driver](https://github.com/adafruit/Adafruit-ST7735-Library) to the nRF51. It can be found [here](https://github.com/adamgreen/Ferdinand20/tree/master/external/Adafruit-ST7735-Library). The above photo shows this driver being used to run a simple test program on [Adafruit's 1.54" 240x240 TFT Display](https://www.adafruit.com/product/3787).

I ran the simple test program on this display and [Adafruit's 1.5" OLED Display](https://www.adafruit.com/product/1431) outside in sunlight to compare their performance. I have a few observations based on my indoor and outdoor testing:
* The TFT LCD display has almost 3.5x the resolution of the OLED.
  * This results in much better image quality.
  * It also results in a slower refresh rate as it takes longer to push the larger number of pixel updates out over the 8MHz SPI bus.
* While the OLED appears brighter indoors, it washes out in the sunlight.
* The TFT LCD isn't quite as bright indoors but outdoors it is still quite visible and only disappears in direct sunlight. Using my hand as shade made the TFT LCD visible again but had minimal impact on the OLED.
* The OLED breakout was supposed to support a Vcc supply of 3 - 6V but in my testing the display blinked a lot when connected to anything less than 5V. I think this was an issue with the regulator used by Adafruit on that breakout. The TFT LCD breakout was successfully powered from the 3.3V supply of the micro:bit.

Based on my testing, I have decided to use the TFT LCD for the Power Distribution Board.

### Motor Power Relay
I wired up the [SparkFun Beefcake Relay Control Kit (Ver. 2.0)](https://www.sparkfun.com/products/13815) and implemented code to energize the relay when the remote BLE deadman switch was depressed. I did need to do two things to get the required 5mA from the nRF51 to the base of the BJT used to energize the relay:
* I had to configure the output pin for high current drive when in the 1 state: ```nrf_gpio_cfg(MOTOR_RELAY_PIN, ..., NRF_GPIO_PIN_S0H1, ...);```
* I replaced R2, the 1k ohm base current limiting resistor, with a 680 ohm resistor to handle the 3.3V digital signal level from the nRF51 instead of the 5V expected in the original Beefcake design.

---
## May 21st, 2020
Wow! It has been around 2.5 months since I last did any work on my Robot-Magellan bot. Now that I have completed my other embedded project, I can turn my attention back to this bot.

### Current Reading List
KiCAD Like a Pro<br>
I have always used [Eagle](https://www.autodesk.com/products/eagle/overview) for designing PCBs for my hobby projects in the past. This project is just as much about learning new things as it is about building a robot to compete in the SRS Robo-Magellan competition. Therefore I think this is a good time to learn [KiCad](https://kicad-pcb.org) and use it for the design of Ferdinand20's custom PCBs. I have started reading [KiCad Like a Pro by Dr. Peter Dalmaris](https://www.amazon.com/dp/B07M9HH2WW) so that I will be ready to make the switch from Eagle by the time I start work on the first PCB for this bot.

### Next Steps
I have a few more things that I want to experiment with before I start designing the PCB for the Power Distribution Board:
* ~~Implement a nRF51 driver for [Adafruit's 1.54" 240x240 TFT Display](https://www.adafruit.com/product/3787) so that I can compare its  performance in sunlight to [Adafruit's 1.5" OLED Display](https://www.adafruit.com/product/1431).~~
<br>Adafruit 1.54" TFT Breakout
* ~~Implement code to switch the motor voltage from the LiPo batteries using [SparkFun's Beefcake Relay Control Kit (Ver. 2.0)](https://www.sparkfun.com/products/13815) and verify that it works as expected.~~
<br>Relay Kit all soldered up

---
## March 7th, 2020
### Catching the Dragon by its Tail
PDB Prototype using Adafruit DragonTails\
I had some time this weekend, while I was between other projects, to switch my micro:bit based Power Distribution Board (PDB) prototypes over to use my recently received [Adafruit DragonTail micro:bit adapters](https://www.adafruit.com/product/3695). I must say that those are really cool additions for prototyping with the micro:bits. I was able to get the joystick module switched over in just a few minutes. Gone were the alligator clips that were barely holding on. Now I had something that I could actually carry around in my hand and use for initial testing. I also added the actual deadman switch to the bottom of the breadboard since I now had access to enough GPIO pins to add it.

Switching the BLE central module over to the DragonTail meant that I now had access to the 5 GPIO pins that I needed to properly connect my [1.5" OLED screen from Adafruit](https://www.adafruit.com/product/1431). Once I had it connected, I was able to finish porting and testing the drivers ([SSD13351](https://github.com/adafruit/Adafruit-SSD1351-library) and [GFX](https://github.com/adafruit/Adafruit-GFX-Library)) for the OLED. My ports of the drivers can be found [here](https://github.com/adamgreen/Ferdinand20/tree/master/external/Adafruit-GFX-Library) and [here](https://github.com/adamgreen/Ferdinand20/tree/master/external/Adafruit-SSD1351-library). Currently I just have it running one of the Adafruit samples. I will later update the code to have the screen show the actual information of interest.

---
## February 20th, 2020
### Adafruit Order Received
Adafruit order arrived<br>
I received my Adafruit order earlier this week. This order included the two [Adafruit DragonTail micro:bit adapters](https://www.adafruit.com/product/3695) that I have been waiting for. These will make it easier for me to interface the OLED screen and relay to my micro:bit board and complete the Power Distribution Board prototype.

This order also included a [1.54" 240x240 Wide Angle TFT LCD Display](https://www.adafruit.com/product/3787) to compare with the [OLED display that I already have](https://www.adafruit.com/product/1431). I am interested to see which one is better for viewing outside in the sun.

I also ordered a [Slamtec RPLIDAR A1 - 360 Laser Range Scanner](https://www.adafruit.com/product/4010). This LIDAR unit is similar to the one that Xandon used on our [Ferdinand14 attempt](https://github.com/adamgreen/Ferdinand14#robopeak-rplidar-sample-in-processing-on-os-x). I don't currently plan to use this unit for 2020 but I saw it on the Adafruit site and thought it would be good to have for future experimentation.

---
## February 17th, 2020
### Received Sparkfun Order
Sparkfun order arrived<br>
This weekend I received the relay parts that I recently ordered from Sparkun and quickly got down to soldering up the [SparkFun Beefcake Relay Control Kit (Ver. 2.0)](https://www.sparkfun.com/products/13815).
<br>Relay Kit all soldered up<br>
I am still waiting for the parts from Adafruit to arrive.

---
## February 12th, 2020
### BLE Central Prototype
#### Basic BLE Central Connectivity to Joystick
Photo of central prototype connected to laptop<br>
After completing the initial proof of concept for the BLE joystick/deadman switch last week, I started writing code to implement a prototype for the BLE central counterpart which will live on the Power Distribution Board (PDB) itself. So far I have only implemented enough code to wirelessly connect to the joystick module and forward the received packets out over the UART. The code for this initial prototype can be found [here on GitHub](software/PDB/BleCentral).

#### Further Progress Stalled
Once I had basic BLE connectivity to the joystick/deadman switch working, I turned my attention to [this 1.5" OLED screen from Adafruit](https://www.adafruit.com/product/1431). Luckily Adafruit has already written a few nice Arduino graphic drivers that work together to drive this display:
* https://github.com/adafruit/Adafruit-SSD1351-library
* https://github.com/adafruit/Adafruit-GFX-Library

I have finished my initial porting attempt to get these Arduino libraries working with the nRF51 SDK and now have them building successfully. When I went to test this code, I hit my first hiccup which I knew was coming at some point. It is easy to connect up to 3 of the GPIO pins on the micro:bit using alligator clips but the rest are smaller card edge connectors. While I could easily solder hookup wires to them, I would like to reuse these micro:bit boards for other projects in the future. Adafruit sells an adapter board that makes it easy to plug the micro:bit into a breadboard. I want to get one of those in my hands before I continue working on this part of the Ferdinand20 project. I also want to order a relay board from Sparkfun to use for prototyping the switching of the motor supply. To this end, I have ordered the following 2 parts to allow for the continuation of this part of the project:
* [Adafruit DragonTail for micro:bit](https://www.adafruit.com/product/3695)
* [SparkFun Beefcake Relay Control Kit (Ver. 2.0)](https://www.sparkfun.com/products/13815)

I will continue working on the PDB prototype again once these parts arrive next week.

### Current Reading List
Photos of books I am currently reading<br>
I plan to use the behavior-based approach for programming this robot. To that end, I am currently rereading these 2 books:
* [Robot Programming : A Practical Guide to Behavior-Based Robotics by Joe Jones](https://www.amazon.com/Robot-Programming-Practical-Behavior-Based-Robotics/dp/0071427783)
* [Cambrian Intelligence: The Early History of the New AI by Rodney A. Brooks](https://www.amazon.com/Cambrian-Intelligence-Early-History-New/dp/0262522632)

---
## February 3rd, 2020
### BLE Joystick Prototype
Photo of BLEJoystick Prototype

Last week I started working on a prototype of the remote portion of the Power Distribution Board (PDB). The current prototype uses a [micro:bit development board](https://microbit.org) that I already had on hand. It is able to read the joystick status (x/y coordinates and switch status) and the battery voltage level to send wirelessly via BLE back to a central device (like the PDB in the future). The current prototype doesn't contain the deadman switch yet but it will be added once I have an easier way to access another of the micro:bit's GPIO pins.

Source code for this prototype has already been pushed to this repository:
* The source code for this prototype's firmware can be found [here on GitHub](software/PDB/BleJoystick).
* The source code for a simple console application that runs on macOS and can display the packets sent from the BleJoystick prototype can be found [here on GitHub](software/PDB/macosTest).

---
## January 31st, 2020
### Power Distribution Board
One thing that I really liked about the [Parallax Arlo Platform](https://www.parallax.com/product/arlo-robotic-platform-system) that I used for my 2016 Robo-Magellan attempt was its [Power Distribution Board](https://www.parallax.com/downloads/arlo-power-distribution-board-product-guide). This board allowed for the separate switching of the main electronic components (microcontrollers, sensors, etc) from that of the power for the motors so that the rest of the electronics could be tested while keeping the bot stationary. It also had fuses for protecting the various circuits.

I would like to have a similar power distribution board (PDB) for my Sawppy rover. My desired feature list includes:
* **Wireless Deadman Switch:** Instead of a physical switch to disable power to the motors, I want it to be wireless instead. To be compliant with the [Robo-Magellan rules](https://robothon.org/rules-robo-magellan/) this switch should be a deadman switch that requires me to actively engage the switch for the rover to enable the power to the motors via a relay. Losing power on the wireless switch, losing wireless connectivity, dropping the switch, or otherwise releasing the switch should disable the motor power.
* **Wireless Joystick for Manual Control:** It would be nice if the same wireless device containing the deadman switch also contained a joystick which could be used for manually driving the rover around. There could be a switch on the power distribution board that enables this manual driving mode and then have some UI on the rover which makes it clear to me and the judges that it isn't in this mode during competition.
* **Nordic nRF51 Powered:** The power distribution board should have built-in intelligence provided by a Nordic nRF5 BLE capable microcontroller. This microcontroller would not only manage the BLE connection to the deadman switch/remote but also monitor the battery voltage, communicate power state to the main microcontroller, and update an onboard screen.
* **LiPO Battery Connector:** A 2S 7.2V LiPo battery would be connected to this power distribution board to provide all of the power required by the bot. This battery input will be fused at 15A.
* **Power outputs:** It should provide terminals for motor power and another set of terminals to power the rest of the electronics. Both outputs will be fused: 10A for the motor terminals and 2A for the electronic terminals.
* **Power Switch:** The power distribution board should have one switch which enables the power to the built-in nRF51 microcontroller and the other electronics but not the motors. That means it doesn't need to switch that much current (would probably be fused at 2A).
* **Motor Power Relay:** By default switching on the power to the bot would only provide power to the electronics and not the motors. To provide power to the motors, the deadman switch must be wirelessly connected and depressed. This would enable the relay controlling power to the motor terminals.
* **Manual Override Switch:** Should also have a switch that allows the joystick on the deadman switch to be used for manually controlling the bot. The fact that the bot is in this mode should be prominently displayed on the screen. When in this mode, the nRF51 microcontroller in the PDB will send joystick update messages to the main microcontroller via the UART connection.
* **Screen:** The power distribution board should have a LCD or OLED screen visible from behind the bot where it will be more visible to judges and me. It will display important status such as LiPo battery voltage, remote control battery voltage, manual/auto drive mode, motor power state, and status messages sent from the main microcontroller via the UART connection.
* **LiPo Battery Monitoring:** The nRF51 microcontroller on the PDB should monitor the LiPo battery voltage. It should report the voltage to the attached screen and automatically warn the user via the onboard screen and disable motor power when the voltage gets too low.
* **Serial Connectivity:** There should be a UART connection between the nRF51 microcontroller on the PDB and the main microcontroller. It will use this connection to send the current deadman switch state on a regular basis (>10 times per second) and joystick status when in manual drive to the main microcontroller. Main microcontroller could even watchdog off of this to send a stop command to all motors if it stopped receiving messages from the PDB. The main microcontroller should also be able to send status text back to the PDB via this UART so that it can be displayed on the screen.

---
## January 24th, 2020
Sawppy Turning InPlace

This week I was able to use [Roger Cheng's](https://github.com/Roger-random) Arduino based control code to implement my own [mbed based SawppyDrive driver](https://github.com/adamgreen/Ferdinand20/tree/master/software/SawppyDrive). The above animation shows this new driver in action. So far the only test code I have is a command line interface that works through the GDB console when remotely connected to Sawppy via BLE but that is enough to already see some nice progress being made on this project:
* The BLE based firmware upload and debugging has proven to be very useful for the development of the code running on the Sawppy so far! I am happy that I put the effort into implementing that functionality earlier in the project.
* It is very cool to see the Sawppy rover actually moving around after having put all that work into building the mechanics over the last couple of months. I was already impressed with Roger's design before but now I am even more impressed as I see my rover actually moving around on its own.
* At this point I consider myself mostly done with the mechanical portions of this project and I will now start concentrating on the electronics.

---
## January 19th, 2020
I took some time off from this project over the holidays but now I am jumping back in where I left off at the end of 2019.

### Current Reading List
Photos of books I am reading

I am currently in the process of reading two books that are related to autonomous vehicles. One about earthbound vehicles and the other about a vehicle currently roaming the surface of Mars:
* [The Design and Engineering of Curiosity: How the Mars Rover Performs Its Job by Emily Lakdawalla](https://www.amazon.com/Design-Engineering-Curiosity-Performs-Springer/dp/3319681443)
* [Creating Autonomous Vehicle Systems by Shaoshan Liu et al.](https://www.amazon.com/Creating-Autonomous-Synthesis-Lectures-Computer/dp/1681730073)

### 4 to 1 Serial Servo Adapter
My 4 to 1 adapter for LX-16A serial connections

During initial testing of my LX-16A serial servo driver code, I only needed a single 3-pin connection from the LPC1768 microcontroller. Now that I have completed the wiring harnesses for the robot, I need to connect 4 such serial cables to the microcontroller. The photo above shows the single female 1x3 header to four male 1x3 header adapter board that I built with a small piece of PCB protoboard. With this in place, I can now send commands and receive responses from all 10 of the LX-16A servos on my [Sawppy rover](https://github.com/Roger-random/Sawppy_Rover).

### My Electronics Mounting Hack
Mounting Hack

The above photo shows how I have hacked the batteries and my current electronics onto the Sawppy base with foam board, tape, and elastic bands. This should suffice for my initial testing.

---
## December 18th, 2019
I haven't been working directly on my Robo-Magellan bot for the last few weeks but I have a good excuse...I promise :) Since I got the [Prusa i3 MK3S printer](https://www.prusa3d.com/original-prusa-i3-mk3/) earlier this year, I have only used it to print existing designs that I downloaded from the Internet, most of which were [Sawppy Rover parts](https://github.com/Roger-random/Sawppy_Rover). I decided to now take the time to learn [openSCAD](https://www.openscad.org) so that I can design and print my own parts.

### openSCAD
OpenSCAD Cookbook<br>

I have skimmed the openSCAD documentation in the past but it is really best used as a reference and isn't really compatible with my learning style. I found that the ["OpenSCAD Cookbook - OpenSCAD Recipes for learning 3D modeling" by John Clark Craig](https://www.amazon.com/OpenSCAD-Cookbook-Recipes-learning-modeling/dp/1790273919)  to be a good introduction for a beginner like myself. It only took me two evenings to read through it and at the end of the second night, I was starting to work on my own designs. When I needed to dig into openSCAD even more I found that the [openSCAD cheat sheet](https://www.openscad.org/cheatsheet), easily launched from within openSCAD's "Help" menu, was a great resource for further learning.

### openSCAD Projects
#### Bose Speaker Stand Plug Replacement
One of the stands for my Bose speakers hasn't been useable for over a decade because of one little cracked plastic plug that mates the vertical rod of the speaker with its base. The first project I tackled after learning openSCAD was to design a replacement for this broken piece. The following photos show the design preview in openSCAD and the final 3D printed object installed in the now fixed speaker stand (black ring where rod meets base).<br>
Plug design in openSCAD<br>
Photo of plug installed<br>
The plug is now functional but there are a few things that I might improve in the future:
* Use a white PETG filament that more closely matches the colour of the speaker stand. Currently the only PETG filament that I have on hand is the black PETG that I used for the Sawppy parts. I have white PLA but the part needed to be a bit more flexible than PLA allows.
* The outer diameter at the top and bottom of the cylinder could be further reduced to allow for a better fit in the speaker base.

#### 2D Calligraphy in 3D
When my Prusa i3 MK3S arrived, it had a black and white print of a "Prusa" name plate on the print bed. It was printed with two different colours of filament which was accomplished by first printing the background in white, pausing the print so that the user could manually unload the white filament to load in the black filament, and then continuing to print the text itself in black. I thought it would be cool to do the same for some of my wife's calligraphy projects so my next project was to load a 2D scan of one such project and extrude it into a 3D print as seen in the following images:<br>
Screenshot of Hope Calligraphy<br>
Photo of Hope Calligraphy

#### NeoPixel Christmas Tree Updates
Previous NeoPixel Tree Version<br>
Last year I built a [NeoPixel Christmas tree](https://github.com/adamgreen/NeoPixelTree#readme) that I really liked the look of but I wasn't completely satisfied with the robustness of the branches and their connections to the LEDs. This year I wanted to design a more robust version and I thought that the 3D printer might be able to play a part in the redesign. The following photo shows the 2-piece cone that I printed out on my printer to provide the form for this new version of the tree. The holes in the cone will be used to hold the [premade strand of NeoPixel LEDs](https://www.amazon.com/WESIRI-Diffused-Individually-Addressable-Waterproof/dp/B075T84ZR3) in place and I plan to cover that all up with artificial pine rope.<br>
Photo of Tree Cone

---
## November 25th, 2019
Last week I started working on the custom wiring harness for the [LewanSoul LX-16A servos](http://www.lewansoul.com/product/detail-17.html) on my [Sawppy rover](https://github.com/Roger-random/Sawppy_Rover#readme). I completed most of the required segments and I thought I would take some time to document my cable building process here so that I have something to refer back to when I next create more cables for these servos or just need to use the crimping tool again.
<br>Wire Harness Supplies
<br>Cable attached to Sawppy

### Prepare Ribbon Cable
I originally ordered 5 feet of the 6-conductor ribbon cable but it turned out that I should have ordered the [10 foot length of ribbon cable](https://www.digikey.com/product-detail/en/3m/8125-06-100/ML06G-10-ND/2658729) instead. 6-conductor cable was chosen as it was easy to get in the 22AWG conductor size that I wanted and is easily 'zipped' in half to produce two 3-conductor cables. I cut segments of the necessary length from the ribbon cable, as documented in the following table:

| Cable | Length |
|---|---|
| Rocker - Front wheel drive servo to front steering servo | 26cm |
| Rocker - Front wheel steering to microcontroller | 43cm |
| Boogie - Rear wheel drive servo to rear steering servo | 26cm |
| Boogie - Rear steering servo to middle fixed wheel drive servo | 48cm |
| Boogie - Middle fixed wheel drive servo to microcontroller | 41cm |

Once I had a segment cut to length, I pulled back the flat white portion of the ribbon cable, separating it from the 3 individual conductors. I did this to reveal 25mm of free conductors as seen in the following photo.

Strip Ribbon Cable<br>

I then cut the excess flat portion of the ribbon cable away and stripped 2mm of the insulation off each of the 3 conductors. This 2mm length was chosen to match the portion of the crimp pin that is supposed to make contact with the bare conductor without being too long and passing into the portion of the pin which later makes contact with the male pins in the LX-16A servo.

Stripped ribbon cable<br>

### Crimping Tool
The [SN-28B ratcheting crimping tool](https://www.pololu.com/product/1928) that I ordered from Pololu arrived a few weeks ago. This is the first time that I have attempted to use such a crimping tool. I found a few videos online that gave me an idea of how to use it:
* [YouTube Video: SN-28B Crimping tutorial for DuPont pins.](https://www.youtube.com/watch?v=-u1t7Cdf6RE)
* [YouTube Video: Pololu Crimper - How to by Ewan](https://www.youtube.com/watch?&v=K7Qb3DzIX3s)

I am not sure that every crimper that I see in videos have the die oriented the same way as mine. Each of the die are held in the crimping tool with a single screw which can be removed so that the die can be reoriented to best accommodate the most current project. To get a feel for which way the pin should be placed in the crimper, I squeezed the tool down through the 5 ratcheting clicks and looked at the die when fully closed. When this is done, it is easy to see that one side squeezes down the pin flaps more than the other:

**Smaller side of die used to squeeze pin around conductor**
Conductor Side of Crimping Tool

**Larger side of die used to squeeze pin around insulation**
Insulation Side of Crimping Tool<br>

### Crimping Pins to Prepared Ribbon Cables
The steps I used for crimping my ribbon cable pins:
* Hold the part of the crimp pin that doesn't take wire in left hand.
* Hold crimper in right hand with larger insulation side of crimping tool facing user.
* Place the crimp in from far side of crimper and let the insulation tabs hook on the top ('M' shaped) part of the crimper where the separation between wire and insulation portion of the die is found.
  * I used the smallest die pattern for the 22 AWG wire, even though Pololu documentation says to use the middle one for this gauge of wire. Using the middle slot resulted in crimped pins that didn't slide into the pin housing properly.
Pin in Crimper
* Ratchet down for 3 clicks to grip the pin.
* Pull on the pin from the other side of the crimper to make sure that the pin is properly seated up against the edge between the insulation and conductor portion of the die.
Pin in Crimper
* Push wire in from larger insulation side of the crimper. Wiggle wire around to make sure that you can just see the ends of the conductors from far side of crimper but not so far that insulation ends up under the tabs that should fold around conductor.
Wire into Pin
* Ratchet down 2 more clicks and continue to squeeze until the tool pops back open. The pin is now complete.
Crimped Pin

### Housings for End of Ribbon Cables
Instead of buying new [3 position housings](https://www.digikey.com/product-detail/en/molex/0050375033/WM18874-ND/280419) to hold the pins at the end of the cables, I reused the ones on the cables that originally shipped with the LX-16A servos. Pushing down on the pins already in the housings made it easy to pull out the existing cables.
<br>Reusing Header<br>
I was then able to insert the crimped pins from the new cables into these housings.
<br>New Cable<br>

---
## November 4th, 2019
### Completing the Sawppy Mechanical Build
There were just a couple of things left to finish with my Sawppy build and to perform them, I had to take the steering and drive portions of the rover apart. These final build steps included:

#### Replacing Servo Coupler Screws
When I first read through the [Sawppy build instructions](https://github.com/Roger-random/Sawppy_Rover), I missed the [note](https://github.com/Roger-random/Sawppy_Rover/blob/master/docs/AssembleActuatorModule.md#install-shaft-coupler) about needing to purchase longer screws for attaching Sawppy's servo couplers to the LX-16A's servo horns. I initially used the short screws that came with the servos since I hadn't ordered the longer ones in my original McMaster-Carr order but they barely gripped the servo horn at all. Once I had completed my initial Sawppy build and knew that I wasn't missing any other parts, I ordered up the missing [longer screws](https://www.mcmaster.com/98685a220). They arrived a few days later and I was able to get them installed.
Longer screws in servo couples

#### Filing 8mm Rods for Set-Screws
The Sawppy build instructions recommend filing flat areas in the 8mm rods so that the set-screws can get better purchase. I didn't perform this step while initially cutting and grooving the rods since I didn't know for sure where the flats should be placed on the rods. I instead put the rover together, including tightening down the set-screws so that they left impressions on the rods. I then used the location of these impressions as indicators where I should file the flats into the rods once I had the drive portions of the rover disassembled.

Filing axles for set-screws<br>
Axles after filing<br>

### Custom Wiring Harness Plans
The wires included with the LewanSoul LX-16A servos are way too short for use on the Sawppy rover. I spent some time this week doing some research to figure out how to best create neat custom length wiring harnesses for these servos. I thought at first that standard servo cable connectors were compatible with these servos and while they probably could be forced into the sockets, they aren't really the correct polarized shape. While further researching this topic, I came across [this forum post on the LewanSoul website](http://www.lewansoul.com/forum/forum.php?mod=viewthread&tid=11277) that describes the actual type of connectors used on these servos. It turns out that they are from the Molex Mini-SPOX™ Low Profile Wire-to-Board Connector System.

| Part | Description |
|---|---|
| [CONN HOUSING 3POS 2.5MM SHROUD](https://www.digikey.com/product-detail/en/molex/0050375033/WM18874-ND/280419) | 3-pin connector housing at end of cables |
| [CONN SOCKET 22-28AWG CRIMP TIN](https://www.digikey.com/product-detail/en/molex/0039000160/WM9661CT-ND/3904983) | Pins to be crimped onto wires and pushed into the connector housing listed above |
| [CONN HEADER VERT 3POS 2.5MM](https://www.digikey.com/product-detail/en/molex/0022035035/900-0022035035-ND/403302) | Mating connector for PCB mounting and also found on the LX-16A servos themselves |

For my cable harness I have decided to:
* Reuse the connector housings from the cables that came with the LX-16A servos. The pins/wires already in them are easily removed with a set of tweezers.
* Use the largest wire size supported by the pins, 22 AWG, to minimize the resistance in these longer wires.
* Purchase 6-conductor ribbon cable that I can 'zip' apart to produce two 3-conductor ribbon cables. A 5 foot roll will therefore result in 10 feet of 3-conductor cable which should be enough for this project.
* Have 4 mating connectors on the control PCB. I will have one set of wires that go to the rockers on either side and another set of wires that go to the bogies on either side.

#### Digikey Parts
| Quantity | Part |
|---|---|
| 60 | [CONN SOCKET 22-28AWG CRIMP TIN](https://www.digikey.com/product-detail/en/molex/0039000160/WM9661CT-ND/3904983) |
| 4 | [CONN HEADER VERT 3POS 2.5MM](https://www.digikey.com/product-detail/en/molex/0022035035/900-0022035035-ND/403302) |
| 1 | [CBL RIBN 6COND 0.100 GRAY 10'](https://www.digikey.com/product-detail/en/3m/8125-06-100/ML06G-10-ND/2658729) |

#### Pololu Crimper
I decided to order a ratcheting action crimper from Pololu. It seemed like the most appropriate combination of price and robustness for this project:

| Quantity | Part |
|---|---|
| 1 | [Crimping Tool: 0.1-1.0 mm² Capacity, 16-28 AWG](https://www.pololu.com/product/1928) |

### Next Steps
* ~~Implement the new wiring harness for the 10 LewanSoul LX-16A servo actuators once the required parts arrive.~~
* ~~Connect my existing mbed-LPC1768 soldered prototype board to the LX-16A servos and port Roger Cheng's existing [Arduino sample code](https://github.com/Roger-random/Sawppy_Rover/tree/master/arduino_sawppy) to run on it.~~
* ~~I have decided to ignore the [Ferdinand16](https://github.com/adamgreen/Ferdinand16/tree/master/firmware/robot) code for now and concentrate on fleshing out the electronics for this rover now that I have the initial mechanical build completed. I want to leave the bulk of the software coding until later in the project and instead concentrate on the parts that I am less experienced with and usually get stuck on (ie. mechanical and electronics).~~

---
## October 29th, 2019
Sawppy Mechanical Build Completed<br>
I finished my [Sawppy build](https://github.com/Roger-random/Sawppy_Rover/tree/master/docs#readme) over the weekend though I still have to work on the electronics before I can test having it move around.

### Next Steps
* ~~Design and implement a wiring harness for the 10 LewanSoul LX-16A servo actuators.~~
* ~~Finish the mechanical build by taking the moving pieces apart and filing flat the areas of the 8mm rods where the setscrews make contact.~~
* ~~Connect my existing mbed-LPC1768 soldered prototype board to the LX-16A servos and port Roger Cheng's existing [Arduino sample code](https://github.com/Roger-random/Sawppy_Rover/tree/master/arduino_sawppy) to run on it.~~
* Code review and get back up to speed on the dead reckoning code that I previously started for [Ferdinand16](https://github.com/adamgreen/Ferdinand16/tree/master/firmware/robot). I can then continue developing and testing this code using my existing Arlo platform inside and outside on smoother terrain until I complete my new [Sawppy](https://github.com/Roger-random/Sawppy_Rover#readme) based chassis.

---
## October 26th, 2019
Parts at Makerspace<br>
Once I had all of the parts required for the Sawppy build ready, I packed them up and took them with me to the weekly makerspace meetup on Thursday. I used this meetup as an opportunity to kick off the final build process and managed to complete the [Servo Actuator Module Assemblies](https://github.com/Roger-random/Sawppy_Rover/blob/master/docs/AssembleActuatorModule.md) while there.

Some notes from building the servo actuator modules:
* I will definitely need to order [longer screws](https://www.mcmaster.com/98685a220) for attaching the servo shaft couplers to the servo horns. I am using the short screws packaged with the LX-16A servos for now but they won't be robust enough for actually running the bot.
* The 2 holes in the servo shaft coupler adjacent to where the threaded heat insert was installed are bulged out a bit and block the installation of the servo horn screws. The bulging appears to have been caused by the process of installing the threaded heat insert. I had to file the holes out for the screws to more easily fit.

---
## October 25th, 2019
In preparation for actually starting the Sawppy build, I have spent the last couple of weeks finishing the preparation of the required parts:

### Soldered Prototype for Servo Test Setup
BLEMRI Prototype<br>
Originally I was using a solderless breadboard with wires hanging off of it for the servo test setup. This prototype included the mbed-LPC1768 microcontroller, Nordic nRF51 based BLE debug interface, LiPo battery hookup, and LX-16A servo connection.

Soldered Prototype<br>
I wanted a more robust solution for this prototype to use while configuring and testing the required 10 servos for the build. To accomplish this goal I created a soldered solution and used an [Adafruit Proto Shield for Arduino](https://www.adafruit.com/product/2077) as its main component. The mbed-LPC1768 was soldered to this shield which then allows it to be easily connected to the Arduino compatible headers on the Nordic nRF51 Development Kit while powering both microcontrollers and the servo from the same LiPo battery. The 3.3V regulation for both microcontrollers is provided by the regulator built into the mbed-LPC1768 board.

### Finished 3D Printing
I finished 3D printing  the last of the parts for the Sawppy build:
* [Differential Parts](https://github.com/Roger-random/Sawppy_Rover/blob/master/docs/Print%20Differential.md)
* [Main Body Box Corners](https://github.com/Roger-random/Sawppy_Rover/blob/master/docs/Print%20Body%20Box%20Corners.md)
* [M3 Nut Installation Tools](https://github.com/Roger-random/Sawppy_Rover/blob/master/docs/Print%20M3%20Installation%20Tool.md)

### Cut Misumi Extruded Aluminum
Cut Misumi Lengths<br>
I used a hacksaw to manually cut all of the required lengths from 2 x [2 meter lengths of Misumi 15mm aluminum extrusion](https://us.misumi-ec.com/vona2/detail/110300465870/).

| First Misumi Piece | Second Misumi Piece |
|---|---|
| 385mm | 245mm
| 385mm | 245mm
| 385mm | 245mm
| 385mm | 238mm
| 245mm | 182mm
| 182mm | 161mm
| | 161mm
| | 122mm
| | 122mm
| | 117mm
| | 117mm
| Total: 1967mm | Total: 1955mm

### Cut and Groove 8mm Steel Rods
Cut 8mm Rods<br>
Using a hacksaw I manually cut the 300mm differential segment from one of the [3' lengths of 8mm steel rod](https://www.mcmaster.com/8920k26-8920K263). I cut all of the other required segments from a second 3' length of 8mm rod. I then used a drill press and hacksaw blade to cut the required grooves into the rods.

---
## October 5th, 2019
I can't believe that I managed to get through all of September without documenting any progress here! I was out of town for a few weeks so that definitely cut into my robot building time. I did however continue to 3D print and post-process more Sawppy parts over the last month.

Printed Parts

I made no real progress on the software side of things but I do hope to make up for that this month.

### Robothon 2019
The Robothon 2019 running of the Robo-Magellan competition occurred today down in Seattle Center, in the shadow of the Space Needle. There were two competitors with great bots for today's run: Dave Mier and Bob Cook.
Dave's Bot
Bob's Bot

While watching today's run, I took some notes of things that I should address with my bot:
* I should have the ability to mark areas on the map as no go areas, such as around trees.
* It would be good to have modes which indicate that the bot should follow asphalt or concrete when going between some waypoints if the camera can be used for such terrain detection.
* Be able to set facing direction at different waypoints since the traffic cone could be behind something you just drove past.
  * They like to hide cones behind rocks, posts, etc.

---
## August 31st, 2019
### OpenMV - First Look
OpenMV IDE Screenshot<br>
I took the [OpenMV H7 camera](https://openmv.io/collections/cams/products/openmv-cam-h7) with me to this week's makerspace meetup and started experimenting with it. It is definitely an impressive little device! Here are a few things that I really like about this camera:
* It supports many more computer vision algorithms than the PixyCam.
  * They even have samples that demo the use of machine learning algorithms. Might it be possible to train a traffic cone recognition network?
* Makes it easy to perform lower level camera setting tweaking such as manually setting or disabling features like the following which caused me some problems on the PixyCam:
  * auto white balance
  * auto gain
  * auto exposure
* Has uSD support which can be used to perform data logging for later analysis or testing of new software.
* Has a way to frame synchronize multiple cameras, making stereo vision possible in the future.

Other interesting OpenMV camera features include:
* It uses the LAB color space for color blob tracking. In theory this should be an improvement over YUV.
* They sell a [Polarizing Filter](https://openmv.io/collections/lenses/products/polarizing-filter) which will probably improve outdoor performance.

I hadn't managed to make a lot of progress with the PixyCam on my previous [Ferdinand16 attempt](https://github.com/adamgreen/Ferdinand16#readme) so I think it makes sense to switch and instead use the OpenMV camera for Ferdinand20.

### Next Steps
* Code review and get back up to speed on the dead reckoning code that I previously started for [Ferdinand16](https://github.com/adamgreen/Ferdinand16/tree/master/firmware/robot). I can then continue developing and testing this code using my existing Arlo platform inside and outside on smoother terrain until I complete my new [Sawppy](https://github.com/Roger-random/Sawppy_Rover#readme) based chassis.

---
## August 22nd, 2019
### LewanSoul LX-16A Servo Teardown
Before reading the [Sawppy rover build instructions](https://github.com/Roger-random/Sawppy_Rover#readme), I hadn't heard of the LewanSoul LX-16A serial bus servos. After playing around with one during the recent development of the mbed driver, I was interested in opening one up to see what makes it tick inside!

#### Screw Removal
Unscrew Servo<br>
The servo is composed of three layers of plastic which are held together by 4 screws. The screws were easily removed with a 00 Phillips head screwdriver. The above photo highlights the location of the 4 screws to be removed.

#### Metal Gear Train
Gear Train#1
Gear Train#2<br>
The first thing I noticed after opening up the servo was its all metal gear train. Most of these gears are non-ferrous but there are some ferrous ones (the one which remained in the front face for example) in the mix as well. There is also an unsealed ball bearing in the front face to support the main drive shaft output.

#### Top of PCB
PCB Top<br>
Most of the electronics for the servo are located on the top surface of the PCB.

##### Microcontroller
Microcontroller<br>
The brains of the servo appears to be this ARM based 32-pin microcontroller. [This forum thread](https://www.rcgroups.com/forums/showthread.php?2278850-BradWii-revolution-%21%21-%28for-toy-quadcopters%29) indicates that the **HL004** marked part is a [Nuvoton Mini54ZAN](https://www.digikey.com/product-detail/en/nuvoton-technology-corporation-of-america/MINI54ZAN/MINI54ZAN-ND/2786710) compatible microcontroller that is also used in some Chinese made toy quad-copters. This is a 24MHz capable Cortex-M0 processor.
<br>Nuvoton datasheet IC Pinout Diagram<br>
**Figure 3.2-2** from the **NuMicro(tm) Mini51 Series Data Sheet** shows the pinout of their 33-pin QFN package and there are a number of pins on the PCB which have been routed in a way consistent with this diagram:
* The Vss pin, pin 12, appears to be routed to a large island of copper, consistent with a ground trace.
* The Vdd pin, pin 28, is routed to a nearby filter capacitor.
* The XTAL1 (pin 11) and XTAL2 (pin 10) pins appear to be routed to a resonator.

16MHz Resonator<br>
I attached my oscilloscope to the resonator output and it appears to be running the microcontroller at 16MHz.

##### Complementary MOSFET Drivers for Motor Control
4606 IC<br>
The two **4606** marked parts appear to be [Complementary MOSFET drivers](http://www.aosmd.com/pdfs/datasheet/ao4606.pdf) which are used to drive each side of the motor high or low. The two 4606 ICs together form an H-Bridge motor controller.

##### NPN Transistors
J3Y Transistor<br>
The two **J3Y** marked parts appear to be [NPN Transistors](https://16748.lightstrade.com/view/516066/J3Y-NPN-SMD-Transistor-S8050.html). The base of one is connected to pin 17 (PWM3) and the other is connected to pin 14 (PWM0). The collectors of both are pulled-up to the battery voltage via 330 ohm resistors. I believe that these are used to translate the output voltage from the microcontroller PWM outputs destined for the gates of the p-channel MOSFETs. Without this translation, the p-channel MOSFETs would never shut-off since the gate to source voltage would always be negative enough to keep them on.

##### UART Driver - Maybe
UART Driver<br>
I tried searching for the part number of this 8-pin chip but never turned up anything conclusive. Here is what I suspect:
* Some of its pins appear to be connected to the UART Rx and Tx pins on the microcontroller.
* Maybe it is something like the [SN74LVC3G07 triple buffer/driver with open-drain outputs](http://www.ti.com/lit/ds/symlink/sn74lvc3g07.pdf).
  * This [simpler buffer](https://www.alibaba.com/product-detail/74LVC1G125GV-SOT23-5-Silk-Screen-V25_60722199693.html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) has the same **V25** marking on it.
  * This type of chip would be a good way to interface a 2-pin UART peripheral to the single wire half duplex serial wire.

#### Bottom of PCB
Bottom of PCB<br>
There are really only two things of note on this side of the PCB:
* The [AMS1117 3.3 linear voltage regulator](http://www.advanced-monolithic.com/pdf/ds1117.pdf).
* The ALPS continuous rotation potentiometer. This is the part which allows for the servo to run in both angular and continuous rotation modes. Most servos have pots with physical stops and continuous rotation requires mechanical disconnection of the pot. This is a more flexible solution as it supports continuous rotations. It however only gives consistent resistances through about 330 degrees of its rotation which is more than good enough for the angular positioning mode of this servo.

#### Headers
Headers Labelled<br>
There are two headers on the PCB. I traced out the pins on these headers to verify my suspicions that they brought out the battery power lines and the SWD debug signals. I have labeled the pins in the above diagram.

---
## August 21st, 2019
### LewanSoul LX-16A Driver for mbed LPC1768
It took me awhile to get back into this project last week but the weekly trip to the local Makerspace on Thursday evening helped to kick off the development of the driver code for the LewanSoul LX-16A Serial Bus Servos.

#### Half Duplex Serial/UART driver for the LPC1768
Since I am going to connect the LPC1768 directly to the LX-16A servos using their single wire serial protocol, I started this driver project by developing a half duplex serial driver for the LPC1768. At one time such a driver was part of the core mbed SDK but it has since been removed. I think this removal happened when they started adding support for more microcontrollers, some for which the driver might have been difficult to port. The original is still probably available somewhere on the mbed site but I decided to quickly code up my own version so that I would better understand its implementation, making it easier to add an async DMA mode in the future if needed. The source code for my driver can be found [here](software/HalfDuplexSerial). A few notes about its development:

* The LPC1768 doesn't require external hardware to switch between transmitting and receiving on the same wire. That single signal wire from the LX-16A servo just needs to be connected to both the Rx and Tx pins of the UART.
* When transmitting, both UART pins (Tx and Rx) will be connected to the UART peripheral. The bytes sent out on the Tx pin will loop back into the Rx pin. My driver reads these looped bytes and discards them while in transmit mode.
* When receiving, the Tx pin is reconfigured by the driver to disconnect from the UART peripheral and connect to the GPIO block instead. The GPIO block configures the pin as an input with high impedance. Now the Rx pin will only receive the bytes sent from the LX-16A servo itself.
* I might revisit this driver in the future to make it async using DMA. That way a large number of transmits to update servo positions / rotation speeds can be done with minimal CPU overhead.

#### LX-16A Servo Driver
Once I had a way to reliably communicate with the LX-16A servo using half duplex serial, I started the development of the LX-16A driver itself. The source code for this driver can be found [here](software/LX16A).

* This driver was split into 2 classes:
  * The LX16A_ServoBus class represents the serial bus to which 1 or more LX-16A servos are connected. A reference to an object of this class is passed into each LX16A_Servo object instantiated. It contains a few broadcasting methods which a developer might want to call directly.
  * The LX16A_Servo class represents an abstraction for a particular LX-16A servo attached to the LX16A_ServoBus. A developer would instantiate one of these objects for each servo with which they want to communicate.
* I tried to expose methods for all of the commands documented by LewanSoul for their LX-16A servos that I thought I might want to use or experiment with in the future. There are a few which weren't implemented but they should be easily added if the need arises.
* I wrote a [test harness](software/LX16A/test) for the driver as well which shows how to use many of the LX-16A servo methods.

### LX-16A Servo Observations
#### Position Reading as Encoder?
The LX-16A has a command, SERVO_POS_READ, for reading out the current servo position. The documentation indicates that this command returns a 16-bit **signed** integer. This made me wonder whether it would return position readings outside of the 0 - 240 degree range to which the servo can be commanded in angle mode so I gave it a shot once I had the basic driver functional. The following output shows the result of calling SERVO_POS_READ while commanding the LX-16A to spin continuously:
```
  Spinning servo in positive direction...
  Position = 1002 (240.48 degrees)
  Position = 1062 (254.88 degrees)
  Position = 1138 (273.12 degrees)
  Position = 1194 (286.56 degrees)
  Position = -190 (-45.60 degrees)
  Position = -107 (-25.68 degrees)
  Position = -19 (-4.56 degrees)
  Position = 67 (16.08 degrees)
  Position = 147 (35.28 degrees)
  Position = 229 (54.96 degrees)
  Position = 305 (73.20 degrees)
  Position = 383 (91.92 degrees)
  Position = 465 (111.60 degrees)
  Position = 551 (132.24 degrees)
  Position = 636 (152.64 degrees)
  Position = 720 (172.80 degrees)
  Position = 799 (191.76 degrees)
  Position = 883 (211.92 degrees)
  Position = 968 (232.32 degrees)
  Position = 1051 (252.24 degrees)
  Position = 1136 (272.64 degrees)
  Position = 1194 (286.56 degrees)
  Position = -188 (-45.12 degrees)
  Position = -96 (-23.04 degrees)
  Position = -17 (-4.08 degrees)
  Position = 69 (16.56 degrees)
  Position = 151 (36.24 degrees)
  Position = 232 (55.68 degrees)
  Position = 310 (74.40 degrees)
  Position = 392 (94.08 degrees)
  Position = 473 (113.52 degrees)
  Position = 560 (134.40 degrees)
  Position = 652 (156.48 degrees)
  Position = 733 (175.92 degrees)
  Position = 812 (194.88 degrees)
  Position = 899 (215.76 degrees)
  Position = 986 (236.64 degrees)
  Position = 1070 (256.80 degrees)
  Position = 1154 (276.96 degrees)
  Position = 1191 (285.84 degrees)
  Position = -164 (-39.36 degrees)
```
These results show that the servo does return positions that exceed the 0 to 240 degree range. It would appear to exceed this range by +/- 45 degrees for a total range of -45 to 285 degrees. I had expected at least +/- 30 degrees since that is the range supported by the SERVO_ANGLE_OFFSET_ADJUST command. This leaves ~30 degrees of the full 360 degree swing unaccounted for. It is during this portion of the swing that it can return inconsistent readings. Many times it returns values close to the -45 or 285 extremes but occasionally it returns angles further away from its true location.

It might be possible to use this position reading as an encoder substitute but it will need to be carefully filtered to predict and correct for the potentiometer discontinuity between 285 and 315 degrees.

#### Continuous Rotation Mode is Open Loop
The LX-16A uses its potentiometer to provide position feedback when running in angle mode but when in continuous rotation mode it appears to run open loop. The commanded rotation speed appears to dictate the PWM duty cycle used and not the actual desired angular velocity. This means that the rover wheels might not all be spinning at the correct speed for the desired turning direction and radius. I would think that this could put some strain on the turning servos. The best solution would probably be to add an encoder to each of the six wheels and use software on the LPC176 to close the loop using PID.

### BLEMRI Dogfooding Results
BLEMRI has worked a champ for wirelessly uploading and debugging the LX-16A servo driver test code. I never encountered any issues with its use during the development and testing of this driver. When I used the ESP8266 version on previous projects, I would sometimes hit issues where **mriprog** would fail to switch from the GDB protocol to the faster serial protocol used by the second stage bootloader. Maybe I corrected the issue when I fixed bugs found in **mriprog** during the development of BLEMRI.

### Next Steps
* ~~Teardown one of my LX-16A servos and see what can be seen.~~
* ~~Start experimenting with my recently purchased OpenMV camera.~~

---
## August 9th, 2019
### More Sawppy Parts Printed
Sawppy parts printed so far<br>
Once I figured out how to successfully slice and print Sawppy's wheels, I started printing some of the other Sawppy parts in between wheel prints. These included:
* [LX-16A Servo Brackets](https://github.com/Roger-random/Sawppy_Rover/blob/master/STL/LX-16A%20-%20Bracket.stl)
  * I have printed half of the 10 brackets required and will use a future print to produce the last 5 at once.
  * I used my 3mmx0.5 thread tap to thread all 4 holes in these brackets.
  * Only 2 holes on the same side needed to be tapped but I did all of them so that if something broke in the field, the other side would be ready as a backup.
* [Wheel Hubs](https://github.com/Roger-random/Sawppy_Rover/blob/master/STL/Wheel%20Hub.stl)
  * I installed the heated thread inserts for the set screws a bit differently than how the Sawppy documentation indicates they should be done since I had some issues keeping the threaded inserts aligned properly when I used that method for the [Servo Coupler](https://github.com/Roger-random/Sawppy_Rover/blob/master/STL/LX-16A%20-%20Coupler.stl):
    * Instead of removing the M3 bolt once the inserts were started, I just loosened it up and used it to check alignment and help correct any misalignment.
  * I used a proper [Heat-Set Insert Installation Tool](https://www.amazon.com/dp/B078K72615) instead of a standard soldering tip for installing the 3 other threaded inserts. I found this tool made it easier to maintain proper alignment of the insert during installation and made quick work of those inserts. <br>Proper tool<br>
* [Fixed Knuckles](https://github.com/Roger-random/Sawppy_Rover/blob/master/STL/Fixed%20Knuckle.stl)
  * Two of these are required, with one being a mirror of the other.
  * I successfully printed both but broke one along the layer separation while attempting to install the bearings. The other now has both of its bearings installed. I will need to print a replacement for the one I cracked.
<br>Cracked Knuckle<br>

### Slicing Sawppy Fixed Knuckle
Like the wheel, it looked like it would be best if I tweaked the slicer settings for the fixed knuckles to make sure that the walls were an even multiple of perimeter extrusions. The modified parameters included:
* Print_Settings/Advanced/Perimeters: 0.47mm
* Print_Settings/Advanced/External_perimeters: 0.47mm
* I didn't disable gap fills on this print since they tended to be located in areas that looked like they would need strength such as around holes close to a perimeter. There were also a lot fewer gap fills needed after setting the perimeter extrusion widths to get an even number of perimeter extrusions.

### Next Steps
* ~~I concentrated on 3D printing this week and let my software work items slide. This upcoming week, I want to continue work on the [LX-16A Servo](http://www.lewansoul.com/product/detail-17.html) software. Now that I know I can successfully send them commands from my mbed based LPC1768, I want to write a half-duplex serial driver to enable 2-way communication with them.~~

---
## August 7th, 2019
### Printed first Sawppy Wheel
First Wheel after Sanding

I have printed the first of six Sawppy wheels. The wheel took 9.5 hours to print on my Prusa i3 MK3S. While it didn't look great when I first pulled it off the print bed, it didn't look too bad after some hand sanding.

### String Theory for PETG
This is what the wheel looked like when the print first completed:
<br>First Stringy Wheel on Print Bed<br>
It contained a massive number of strings inside the wheel. Stringing is a common issue with PETG but I didn't expect it to be that bad. I looked through the Prusa forums and I didn't see anyone complain about PETG stringing issues like this.

The wheel is functional but it needed some post-processing. I cut away some of the strings inside of the wheel with a X-acto knife. Once the really long strings were gone, I hand sanded the inside of the wheel to remove more of the strings and smooth out any imperfections they left on the inner surface. The few strings I found on the outside were easily melted away with 200C hot air.

I spent Saturday evening and most of Sunday trying out different things in an attempt to address this stringing issue.
* I started by trying to reproduce the problem on a smaller print that would allow for quicker iterations. To that end, I began by experimenting with these [Retraction Towers from Thingiverse](https://www.thingiverse.com/thing:2867033) created by user [jpasternack](https://www.thingiverse.com/jpasternack).
  * This print (at 0.3mm layer resolution) had a few strings on it by the end of a print with default settings but it was nothing like the wheel. The most obvious abnormality were bumps on the inside of the towers where it appeared that strings had pulled away from the surface as the head moved away to the other tower.
  * I tried increasing the retraction settings to 1.2mm at 40mm/s but this actually resulted in more obvious stringing, not less.
  * I was going to try experimenting with a few lower temperatures on these retraction towers as well but ended up using a different test print for temperature testing. I will discuss that a bit later.
* While researching PETG stringing, I came across [this great YouTube video](https://www.youtube.com/watch?v=8_adY2K-YIc) by [Thomas Sanladerer](https://www.youtube.com/channel/UCb8Rde3uRL1ohROUVg46h1A). It has some great recommendations on things to try tweaking for better PETG printing, including:
  * Increasing retraction length.
  * Modifying retraction speed. Try faster and even **SLOWER** speeds to see what impact they have.
  * Lower extruder temperature.
  * Dropping fan speed range to 20%-50%.
  * Increasing the travel speed when moving from one point to another point while not actively extruding any plastic. He actually recommends that this be set to the maximum speed possible for your printer. When investigating this setting in PrusaSlicer, I realized that it was already set pretty high but my running of the printer in its *Stealth* mode was probably halving the rate actually achieved at print time. Based on this, I printed the retraction towers again with the printer in *normal* mode and the resulting print was very clean and just had the one string from the final pull away with no bumps on the insides of the towers.
  <br>Retraction Tower printed in Normal mode<br>
* When Roger Cheng, the creator of the Sawppy Rover, first printed his PETG wheels, he too [saw massive stringing](https://newscrewdriver.com/2018/07/11/problems-printing-petg-with-monoprice-maker-select-wanhao-duplicator-i3/).
<br>Roger's stringy wheel<br>
He narrowed it down to bad layer adhesion and not retraction. Not only were his prints stringy, they were also weak and the layers separated easily. My prints appear to be quite strong but I still found one statement in his writeup that I think does apply to my situation, "Once this print gets above the first 20mm and no longer printing the center hub, it no longer performs any retracts – the wheel is printed in a continuous motion without retracts." I was seeing a large number of retracts all throughout the print. This caused me to go back and reread [his wheel printing notes](https://github.com/Roger-random/Sawppy_Rover/blob/master/docs/Print%20Wheel.md) to find this statement which I had previously just glossed over, "The wheel spoke and perimeter is an even multiple of nozzle diameter and should print in a few large continuous motions. But the thin dimensions could confuse some slicers. If it generates paths broken up into an excessive number of segments, adjust your slicer settings." I tried a number of things in [PrusaSlicer](https://www.prusa3d.com/prusaslicer/) but the 3 settings that worked to generate nice continuous motions and reduce retractions were:

| Setting | Old Value | New Value
|---|---|---
| Print_Settings/Advanced/Extrusion_Width/Perimeters | 0.5mm  | 0.47mm
| Print_Settings/Advanced/Extrusion_Width/External_perimeters | 0.5mm | 0.47mm
| Print_Settings/Speed/Gap_fill |40 | 0

* During my experimentation, I switched to using these [Temperature Towers from Thingiverse](https://www.thingiverse.com/thing:2893943) created by [Simplify3D](https://www.thingiverse.com/Simplify3D) to see how temperature impacted the PETG printing process. The stringing experienced with this print was really bad over the 240-260C temperature range recommended for my PETG filament. No temperature made it better but the features on the tower sides were best at the 250C used by PrusaSlicer's PETG profile. To have different layers of this tower printed at different temperatures, I added the following to PrusaSlicer's Printer_Settings/Custom_G-code/After_layer_change_G-code setting:
```
{if layer_z==0.2}M104 S240{endif}
{if layer_z==10.0}M104 S242{endif}
{if layer_z==20.0}M104 S245{endif}
{if layer_z==30.0}M104 S247{endif}
{if layer_z==40.0}M104 S250{endif}
{if layer_z==50.0}M104 S252{endif}
{if layer_z==60.0}M104 S255{endif}
{if layer_z==70.0}M104 S257{endif}
```
<br>Bad at all temps<br>

Based on what I have seen with the Retraction/Temperature Tower experiments and Sawppy Wheel prints I think it is the frequency of retractions which are the biggest contributor to my stringing issues. I think the Retraction Towers don't string much because the print head takes awhile to print one of the towers before it needs to retract and travel to the other. The Temperature Tower and poorly sliced versions of the wheel have frequent retractions and correspondingly the worst stringing. Maybe the hot filament doesn't like being compressed and then stretched multiple times when a print in undergoing frequent retractions?

### Onward to More Wheels
In the end I made a few changes before printing the subsequent wheels to improve the quality and speed of the print based on my day of experiments:

* Modified a few PrusaSlicer settings:
  * Print_Settings/Advanced/Extrusion_Width/Perimeters: 0.47mm
  * Print_Settings/Advanced/Extrusion_Width/External_perimeters: 0.47mm
  * Print_Settings/Speed/Gap_fill: 0 (disable)
  * Print_Settings/Infill/Only_retract_when_crossing_perimeters: Enabled
  * Print_Settings/Infill/Fill_pattern: Rectilinear - This improves print speed but I might find it makes the print weaker during future field testing.
* Moved the printer into a room with less air movement.
* ~~Ran the printer in Normal mode instead of Stealth mode.~~<br>
*Later experimentation has since shown that this modification isn't required.*

The build time for each wheel is now down to just under 8 hours with minimal stringing. The inside of the wheels are now very smooth and shiny.

Latest Wheel Print

---
## August 3rd, 2019
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

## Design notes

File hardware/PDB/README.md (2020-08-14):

# Bill of Materials
Description | Quantity | Part Number(s)
------------|----------|---------------
[1N4148WT Diode](https://www.digikey.com/product-detail/en/1N4148WT/1N4148WTCT-ND) | 1 | D1
[Dynastream N5 ANT/BLE SoC Module](https://www.digikey.com/product-detail/en/N5150M5CD/1094-1021-ND) | 1 | U3
[MIC5205 Linear Regulator - 3.3V 150mA SOT23-5](https://www.digikey.com/products/en?keywords=576-1259-1-ND) | 1 | U1
[L4931ABD50-TR Linear Regulator - 5V 250mA](https://www.digikey.com/product-detail/en/L4931ABD50-TR/497-1156-1-ND) | 1 | U2
[MMBT2222ALT3G NPN Transistor](https://www.digikey.com/product-detail/en/MMBT2222ALT3G/MMBT2222ALT3GOSCT-ND) | 1 | Q1
[SMAJ4739A-TP Zener Diode](https://www.digikey.com/product-detail/en/SMAJ4739A-TP/SMAJ4739A-TPCT-ND) | 1 | D2
[0.1uF Capacitor](https://www.adafruit.com/product/441) | 1 | C1
[470pF Capacitor](https://www.digikey.com/product-detail/en/CC0805KRX7R9BB471/311-1124-1-ND) | 1 | C2
[1uF Capacitor](https://www.adafruit.com/product/441) | 4 | C3, C4, C5, C6
[680 ohm Resistor](https://www.adafruit.com/product/441) | 1 | R1
[1k ohm Resistor](https://www.adafruit.com/product/441) | 2 | R2, R3
[Fuse Holder 20A Circuit Blade Surface Mount](https://www.digikey.com/product-detail/en/3587TR/36-3587CT-ND) | 3 | F1, F2, F3
[Female Header for LCD 1x12 - 0.1" Through-Hole](https://www.digikey.com/product-detail/en/chip-quik-inc/HDR100IMP40F-G-V-TH/HDR100IMP40F-G-V-TH-ND) | 1 | J2
[Molex_SPOX_5267-04A_1x04_P2.50mm_Vertica](https://www.digikey.com/product-detail/en/0022035045/WM18888-ND) | 1 | J4
[Molex_SPOX_5267-03A_1x03_P2.50mm_Vertical](https://www.digikey.com/product-detail/en/0022035035/900-0022035035-ND) | 2 | J5, J6
[Sparkfun SPDT-JQX-15F Relay](https://www.sparkfun.com/products/10924) | 1 | K1
[Adafruit 1.54" 240x240 Wide Angle TFT LCD Display](https://www.adafruit.com/product/3787) | 1 | J2
[Metal Pushbutton - Latching (16mm, Green)](https://www.sparkfun.com/products/11973) | 1 | J5
[Toggle Switch and Cover - Illuminated (Red)](https://www.sparkfun.com/products/11310) | 1 | J6
[XT60 Connectors - Male/Female Pair](https://www.sparkfun.com/products/10474) | 1 | J1
[Deans Connectors - Male/Female Pair](https://www.digikey.com/product-detail/en/PRT-11864/1568-1659-ND) | 1 | J3

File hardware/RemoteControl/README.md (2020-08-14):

# Bill of Materials
Description | Quantity | Part Number(s)
------------|----------|---------------
[Dynastream N5 ANT/BLE SoC Module](https://www.digikey.com/product-detail/en/N5150M5CD/1094-1021-ND) | 1 | U1
[Tactile Momentary NO Right Angle Switch](https://www.digikey.com/product-detail/en/PTS645VM13SMTR92LFS/CKN10828CT-ND) | 1 | S2
[Thumb Joystick](https://www.sparkfun.com/products/9032) | 1 | S1
[2 x AAA Battery Holder](https://www.digikey.com/product-detail/en/SBH421AS/SBH421AS-ND) | 1 | Batt+ / Batt-

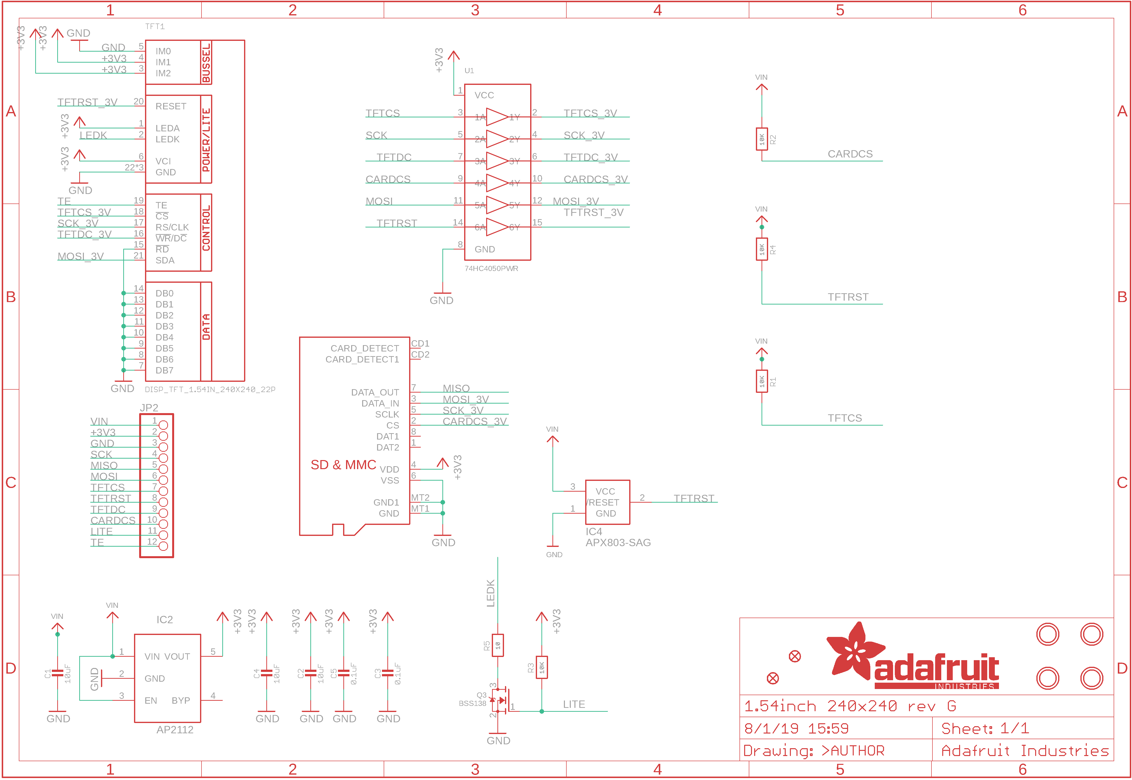
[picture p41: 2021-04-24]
docs/Adafruit_1.54"_240x240_LCD_Breakout_Schematic.png

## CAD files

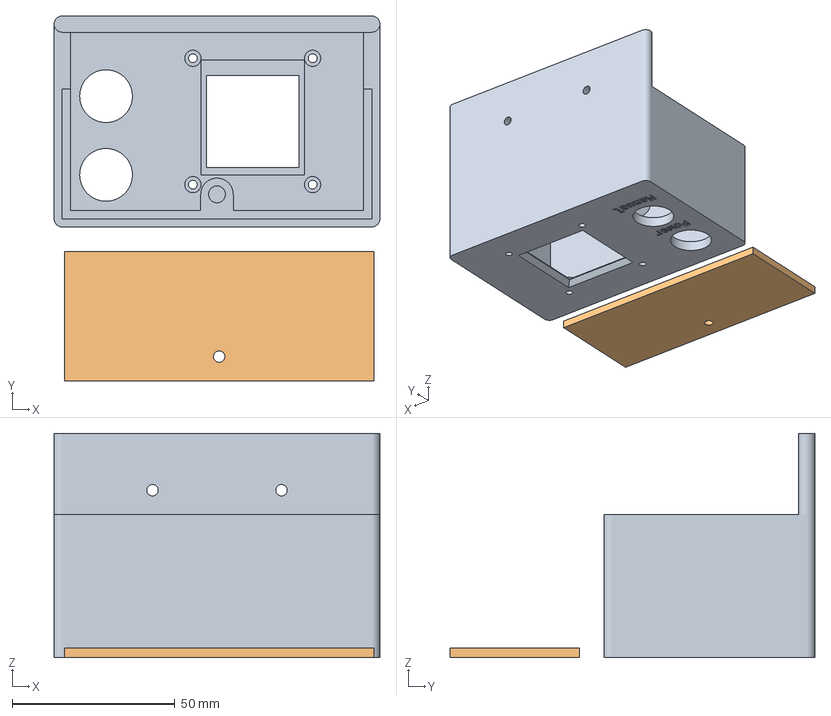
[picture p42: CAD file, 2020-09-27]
cad/PDB/PDB.3mf
100.2 x 112.3 x 69.0 mm
PDB.stl
Door.stl

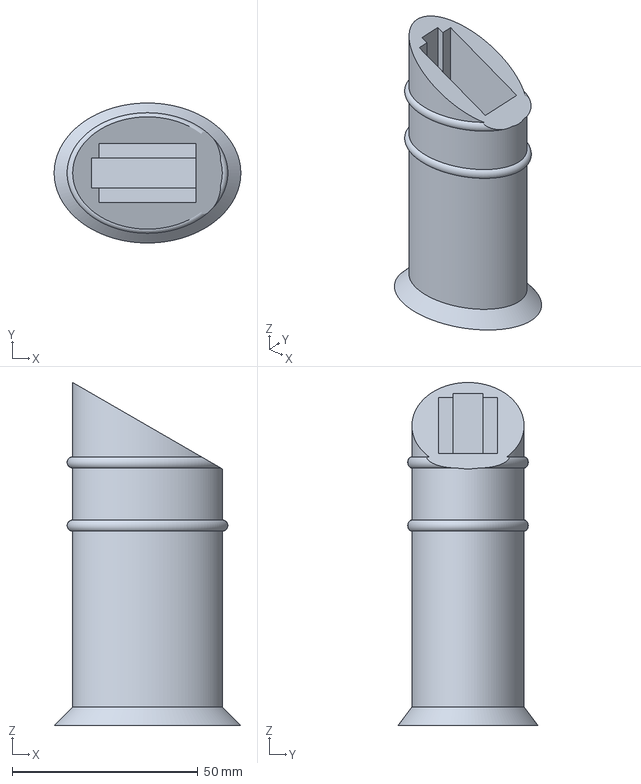
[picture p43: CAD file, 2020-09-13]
cad/RemoteControl/Handle.3mf
50.2 x 37.7 x 92.3 mm

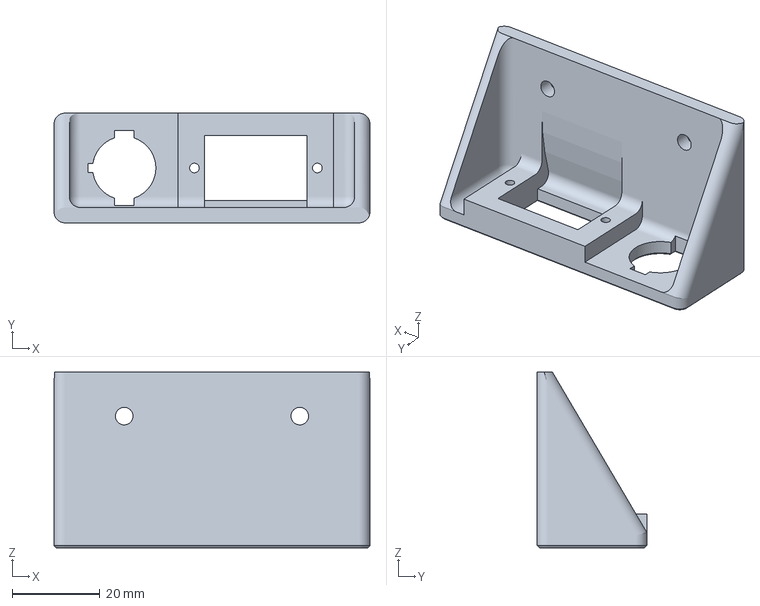
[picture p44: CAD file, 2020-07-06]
slicer/Power Panel.3mf
72.0 x 25.0 x 40.0 mm

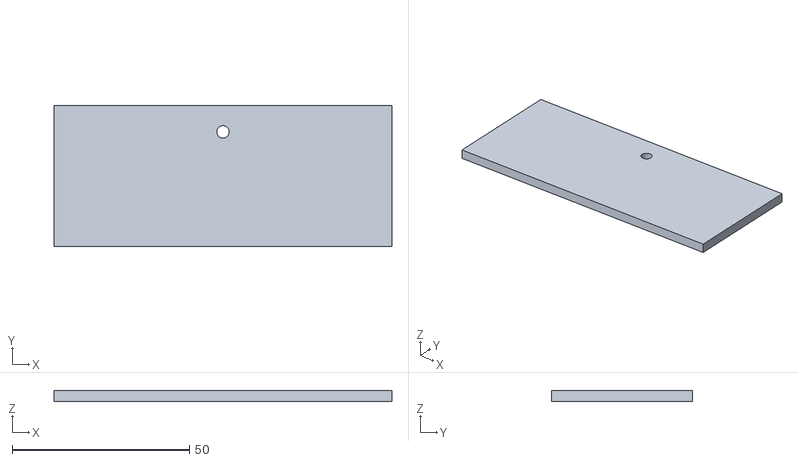
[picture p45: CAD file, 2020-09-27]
cad/PDB/Door.stl
95.2 x 39.9 x 3.00

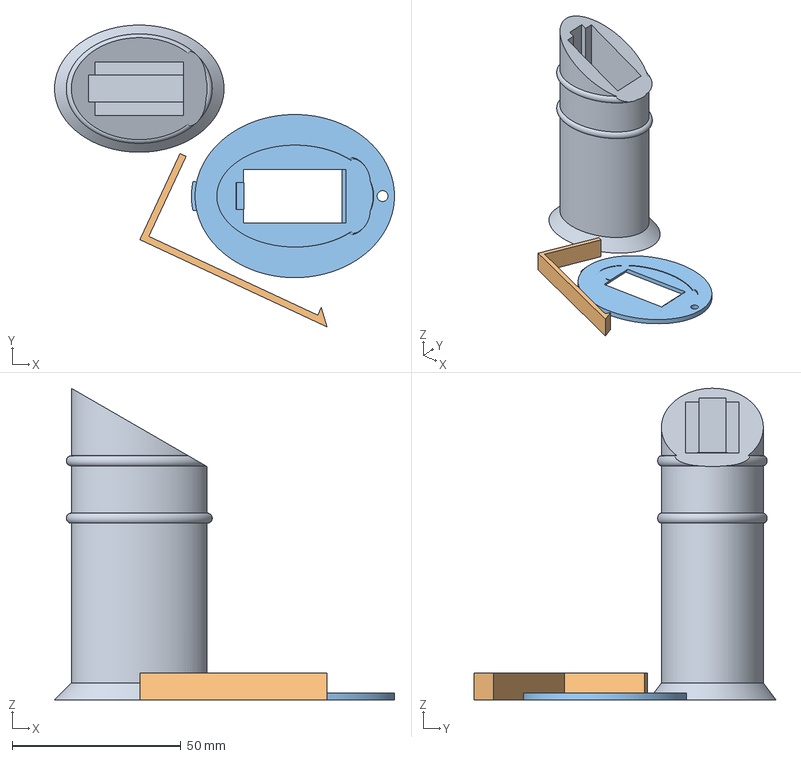
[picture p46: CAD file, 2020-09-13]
cad/RemoteControl/HandleAll.3mf
100.7 x 89.4 x 92.3 mm
Handle.stl
BatteryClip.stl
HandleOval.stl

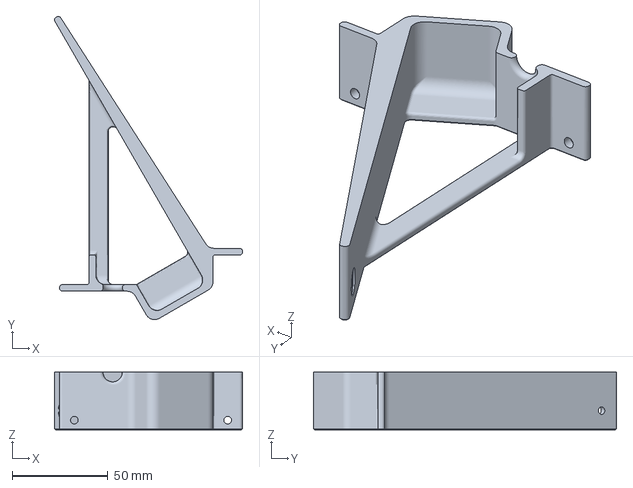
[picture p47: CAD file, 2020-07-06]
slicer/Battery Tray_MIrrored.3mf
98.0 x 158.1 x 30.0 mm

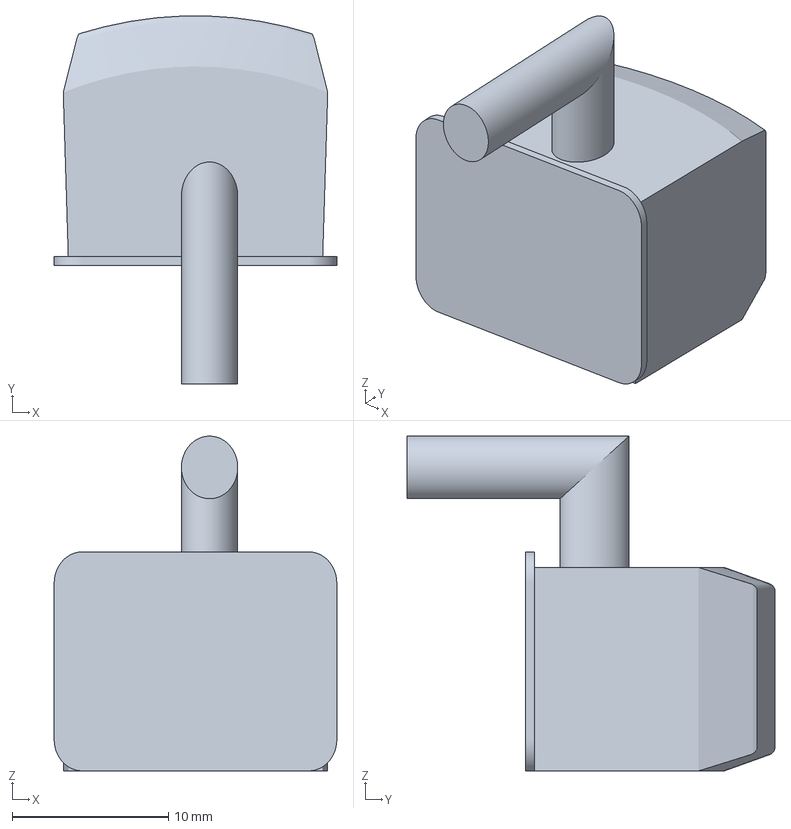
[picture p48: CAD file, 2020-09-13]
cad/RemoteControl/Button.3mf
18.1 x 23.5 x 21.4 mm

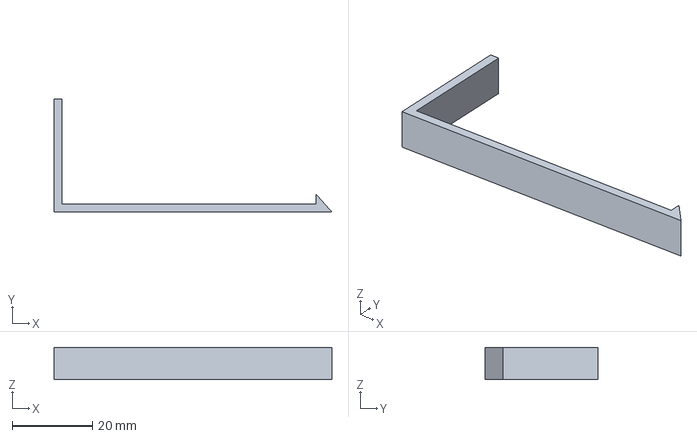
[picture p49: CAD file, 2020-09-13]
cad/RemoteControl/BatteryClip.3mf
69.2 x 28.1 x 8.00 mm

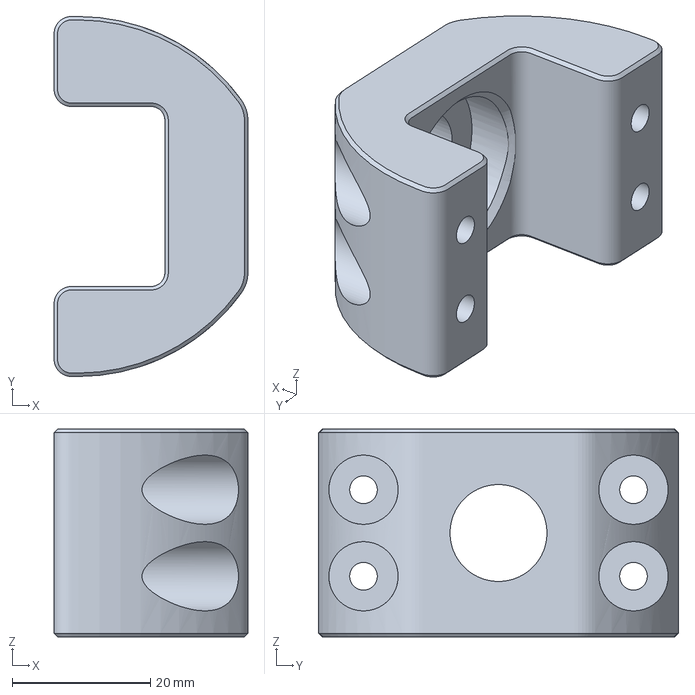
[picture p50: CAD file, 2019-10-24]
slicer/DiffUpper.3mf
28.0 x 52.0 x 30.0 mm

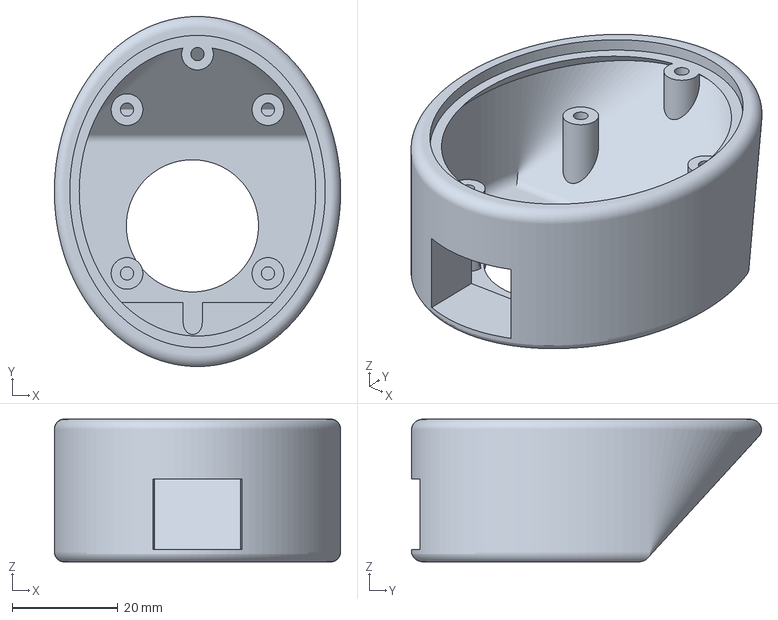
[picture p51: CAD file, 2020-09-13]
cad/RemoteControl/Top.3mf
54.2 x 66.2 x 27.0 mm

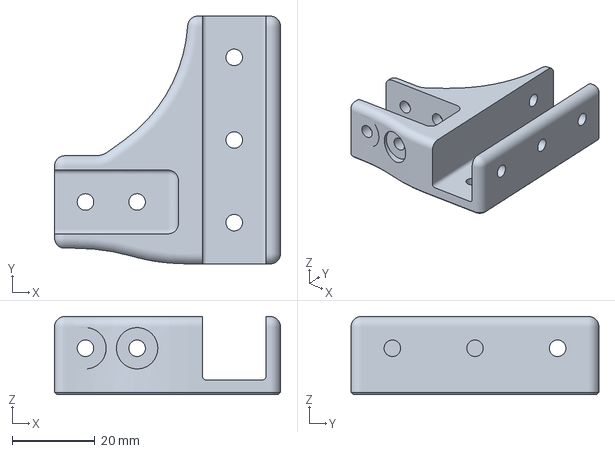
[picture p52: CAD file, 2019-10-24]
slicer/DiffEnd.3mf
54.7 x 60.0 x 18.9 mm

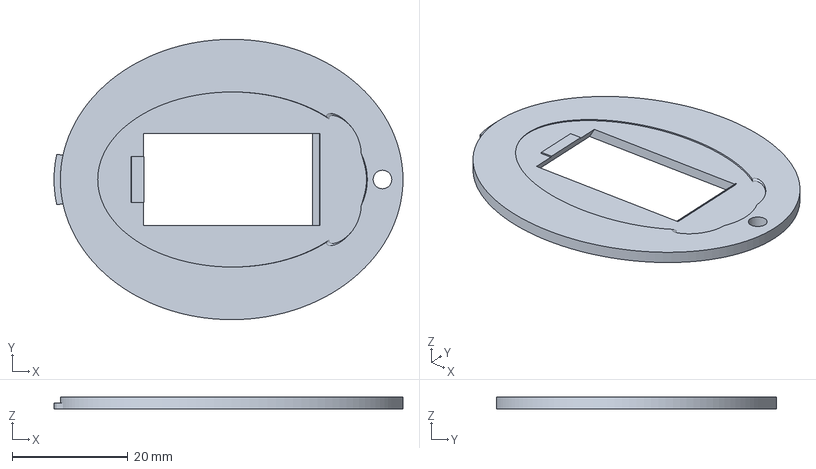
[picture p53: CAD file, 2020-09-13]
cad/RemoteControl/HandleOval.3mf
60.2 x 48.3 x 2.00 mm

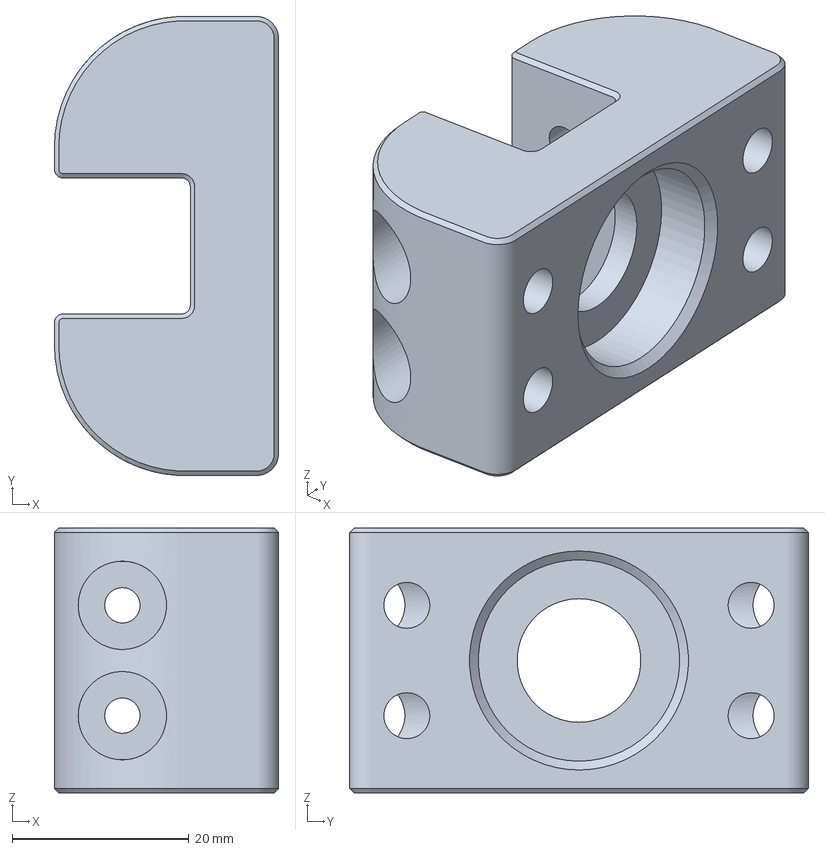
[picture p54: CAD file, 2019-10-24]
slicer/DiffLower.3mf
25.4 x 52.0 x 30.0 mm

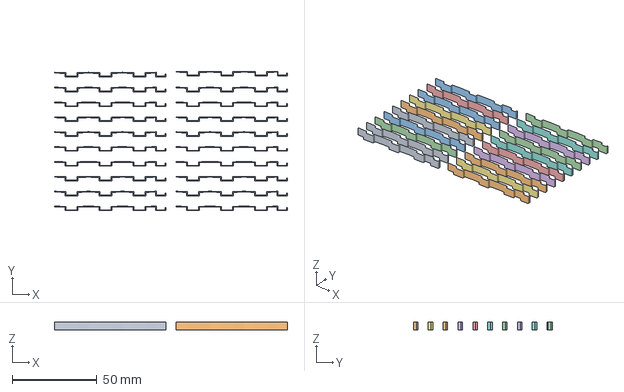
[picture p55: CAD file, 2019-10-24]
slicer/Clip3n20_20x.3mf
137.1 x 82.1 x 4.80 mm

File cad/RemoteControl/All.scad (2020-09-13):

/*  Copyright (C) 2020  Adam Green (https://github.com/adamgreen)

    This program is free software; you can redistribute it and/or
    modify it under the terms of the GNU General Public License
    as published by the Free Software Foundation; either version 2
    of the License, or (at your option) any later version.

    This program is distributed in the hope that it will be useful,
    but WITHOUT ANY WARRANTY; without even the implied warranty of
    MERCHANTABILITY or FITNESS FOR A PARTICULAR PURPOSE.  See the
    GNU General Public License for more details.
*/
// Case to contain the electronics for the remote control.
include <Common.scad>


// Animate in and out by setting anim to 0.0-1.0-0.0
anim = $t <= 0.5 ? $t*2 : (1.0-$t)*2;

// Draw the top of the remote control.
%RemoteControlTop();
// Insert mock PCB inside of controller for size check.
translate([0, 0, pcbZ]) PcbWithJoystick();

// Animate  the deadman button in and out of the front of the controller.
%translate([0, 0.5*anim, 0])
    scale([bodyWidthScale, bodyLengthScale, 1.0])
        translate([0, 0, buttonZPos]) 
            rotate([0, 0, 180]) 
                Button();

// Animate the handle up and down.
%translate([0, 0, -20.0*anim])
    rotate([rampAngle, 0, 0])
        translate([0, 0, -(batteryPackHeight + tan(rampAngle)*batteryPackWidth/2 + 2 * heightClearance)])
            rotate([0, 0, 90]) {
                RemoteControlHandle();
                translate([0, 0, handleHeight-rampHeight-handleIndent]) 
                    rotate([0, rampAngle, 0])
                        DrawTopOval();
                // Insert the battery pack into the middle of the pack for fitment check.
                translate([0, 0, heightClearance])BatteryPack();
        }

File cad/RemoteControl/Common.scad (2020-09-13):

/*  Copyright (C) 2020  Adam Green (https://github.com/adamgreen)

    This program is free software; you can redistribute it and/or
    modify it under the terms of the GNU General Public License
    as published by the Free Software Foundation; either version 2
    of the License, or (at your option) any later version.

    This program is distributed in the hope that it will be useful,
    but WITHOUT ANY WARRANTY; without even the implied warranty of
    MERCHANTABILITY or FITNESS FOR A PARTICULAR PURPOSE.  See the
    GNU General Public License for more details.
*/
// Parameters and modules used to produce multiple parts of the remote control enclosure.
use <Sparkfun_9032.scad>

// **********
// Parameters
// **********
// Dimensions of the PCB to be fit within the top of the remote control.
pcbWidth = 33.0;
pcbLength = 43.0;
pcbThickness = 1.6;
// The top of the remote control is actually an oval created by scaling with these values.
bodyWidthScale = 0.9;
bodyLengthScale = 1.1;
// The amount of free space that should exist around the PCB within the enclosure.
pcbClearance = 3.0;

// The total height of the remote control top. Doesn't include the handle.
bodyHeight = 27.0;
// The radius of the rounded edges used on the remote control top so that there are no sharp edges.
bodyEdgeRadius = 2.0;
// Distance from center of top where the palm slant should start.
bodySlantStart = 9.0;

// How much to scale up the deadman button before using it to cutout a hole for it in the remote control top.
buttonHoleTolerance = 1.03;

// The diameter of the hole at the top of the remote control through which the joystick protrudes.
joystickHoleDiameter = 25.0;

// Dimensions of the lip placed around the large hole in the bottom of the remote control top.
// The handle will have a matching piece to mate with this lip.
// The thickness of the oval at the top of handle which mates with the remote top.
handleLipThickness = 2.0;
// The amount of lip that the handle should come into contact with.
handleLipWidth = 2.0;
// The lip starts this far from the outer diameter of the remote control top.
handleLipStart = 1.25;
// The lip isn't just an overhang. It slops up from the interior sides of the top at this angle.
handleLipSlopeAngle = 45.0;

// Outer diameter of the 4 PCB standoffs in the remote control top.
pcbStandOffOD = 6.0;
// Inner diameter of the 4 PCB standoffs in the remote control top.
// Currently set to be tapped for M3 screw.
pcbStandOffID = 2.5;
// Large value used when it doesn't matter exactly how long something is since it will 
// be booleaned with something else to restrict object to proper length.
longLength = 100.0;
// How far the M3 bolt can be screwed into the standoff.
pcbStandOffHoleHeight = 8.0;
// The PCB is centered in the remote control top. 
// Its standoffs are offset by these amounts in the X and Y axis.
pcbStandOffX = 26.67;
pcbStandOffY = 30.988;
// How far the bottom of the PCB should be from the bottom of the remote control top.
pcbZ = 9.0;

// The deadman button subtends this angle on the outer surface of the enclosure.
// Must be small enough that the resulting button will pass between the PCB standoffs when pressed.
buttonAngle = 30.0;
// The rounded edge between the flat front of the button and the angled edges.
buttonEdgeRadius = 0.5;
// The thickness of the angled part of the button that extends outside of the enclosure.
buttonThickness = 3.0;
// The angled part of the button is this much larger buttonThickness mm from the front surface of the button.
buttonSlant = 1.0;
// The height of the button. If it is too large, it won't fit above the PCB on the standoffs.
buttonHeight = 11.0;
// The button should be centered at this height from bottom of the remote control top.
buttonZPos = 18.0;
// How far should the button be guided inside of the enclosure.
// The simple square part of the button that goes inside the enclosure will be this length too.
buttonGuideDepth = 9.5;
// Dimensions of the flange on the inside of the button which stops the button from falling out of the enclosure.
buttonFlangeWidth = 1.0;
buttonFlangeOffset = 0.0;
buttonFlangeThickness = 0.5;
// Dimensions of the arm which extends out of the bottom of the button to make contact
// with the deadman switch on the PCB.
// NOTE: These dimensions were selected to have the arm line up properly with the
//       deadman switch on the PCB.
buttonArmRadius = 2.0;
buttonArmHeight = 8.4;
buttonArmLength = 10.9;
buttonArmXOffset = -1.0;
buttonArmYOffset = 1.5;

// Dimensions of the 2xAAA battery pack that goes inside the handle.
batteryPackWidth = 25.9;
batteryPackThickness = 15.64;
batteryPackHeight = 63.2;
// Width and thickness clearance around battery pack.
sideClearance = 5.0;
// Height clearance around battery pack.
heightClearance = 5.0;
// The remote control handle is actually an oval created by scaling with these values.
handleXScale = 1.0;
handleYScale = 0.75;

// Diameter of rings around handle to act as grip between fingers.
fingerRingDiameter = 3.0;

// Distance from top for each finger ring.
fingerRingHeights = [21.5, 21.5+17];

// Bottom flange dimensions.
flangeHeight = 5.0;
flangeWidth = 5.0;
flangePoints = [[0, 0], [0, flangeHeight], [flangeWidth, 0]];

// How angled should the handle be with respect to the top of the remote.
rampAngle = 30.0;
// The depth of the indent in the top oval used to mate with the main handle.
handleIndent = 0.25;

// The amount of extra negative space to leave for the battery pack to fit into the handle.
handleBatteryPackClearance = 0.25;
// The dimensions of the snap hook used to hold the battery pack in.
batteryHookWidth = 8.0;
batteryHookTotalHeight = 15.0;
batteryHookArmThickness = 2.0;
batteryHookThickness = batteryHookArmThickness + 2.5;
batteryHookHeight = 4.0;
// The desired clearance around the battery hook.
batteryHookClearance = 1.0;

// The thickness of the tongue between handle and top.
handleTongueThickness=handleLipThickness/2;
handleTongueDepth=1.0;
handleTongueAngle=20.0;




// *****************************************************************
// Top of Remote Control - Holds PCB, joystick, and deadman button.
// *****************************************************************
// Calculated Values
// -----------------
// The distance from one corner of the PCB to other corner.
pcbDiameter = sqrt(pcbWidth*pcbWidth + pcbLength*pcbLength);
// The top of the remote control diameter is based on the PCB dimensions + specified clearance amount.
topDiameter = pcbDiameter + 2 * pcbClearance;
topRadius = topDiameter / 2;
// How wide is the palm rest slant where it starts at the top of the remote control.
bodySlantLength = 2 * sqrt(pow(topRadius, 2) - pow(bodySlantStart, 2));
// How high up into the inside of the enclosure does the lip have to start based on the desired angle?
handleLipSlopeHeight = (handleLipWidth+handleLipStart)*tan(90.0-handleLipSlopeAngle);


// Draws the top of the remote control.
module RemoteControlTop() {
    difference() {
        union() {
            // Use scale to convert circles into desired oval shape.
            scale([bodyWidthScale, bodyLengthScale, 1.0]) {
                difference() {
                    union() {
                        difference() {
                            // The outside shape of the remote control top.
                            // Holes for things like joysticks and deadman button will be removed later.
                            MainBody();
                            // Hollow it out and leave ~2mm of shell.
                            translate([0, 0, -2.0]) scale([0.93, 0.93, 1.0]) MainBody();
                        }
                        // Add extra support inside of the shell to support the deadman button.
                        ButtonGuide();
                        // Add a lip on the bottom of the remote control into which the handle will mate.
                        intersection() {
                            // Use intersection to just keep parts which fall inside of the main body.
                            MainBody();
                            LipForHandle();
                        }
                    }
                    // Make hole for button and its arm to pass through.
                    // NOTE: Not leaving any tolerance on the sides. Sand down the final button to make it
                    //       fit but stay tight enough that it can't tilt off axis and jam when pressed.
                    translate([0, 0.01, buttonZPos]) rotate([0, 0, 180]) {
                        scale([1.0, 1.0, buttonHoleTolerance]) {
                            Button();
                            ButtonArmSlot();
                        }
                    }

                }
            }
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

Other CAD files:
slicer/Battery Tray.3mf
slicer/RodSupport_2x.3mf
slicer/Body Corner.3mf
slicer/DiffLink_2x.3mf
cad/RemoteControl/BatteryClip.scad
cad/RemoteControl/Button.scad
cad/PDB/Common.scad
cad/PDB/Door.scad
cad/PDB/PDB.scad
cad/PDB/PDB.stl
cad/RemoteControl/BatteryClip.stl
cad/RemoteControl/Button.stl
cad/RemoteControl/Handle.scad
cad/RemoteControl/Handle.stl
cad/RemoteControl/HandleOval.scad
cad/RemoteControl/HandleOval.stl
cad/RemoteControl/Sparkfun_9032.scad
cad/RemoteControl/Top.scad
cad/RemoteControl/Top.stl
cad/pot/pot.scad
slicer/Bogie-Body.3mf
slicer/Bogie-Body_Mirrored.3mf
slicer/Bogie-Wheels.3mf
slicer/Bogie-Wheels_Mirrored.3mf
slicer/Clip2n125_50x.3mf
slicer/DiffBrace.3mf
slicer/DiffEnd_Mirrored.3mf
slicer/Fixed Knuckle.3mf
slicer/Fixed Knuckle_Mirrored.3mf
slicer/Front Corner.3mf
slicer/Front Corner_Mirrored.3mf
slicer/LX-16A - Bracket_5x.3mf
slicer/LX-16A - Bracket_Spare.3mf
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

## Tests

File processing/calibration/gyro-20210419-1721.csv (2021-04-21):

temperature | x | y | z
248.3035 | -5.389833333333334 | 2.517 | 3.716666666666667
250.59833333333333 | -3.7071666666666667 | 2.3978333333333333 | 4.4215
252.80383333333333 | -2.0328333333333335 | 2.4595 | 5.1525
224.80683333333334 | 0.17383333333333334 | 2.9555 | 5.9015
0.807 | 2.962833333333333 | 4.6105 | 7.461333333333333
2.4665 | 1.4386666666666668 | 4.196166666666667 | 4.0616666666666665
4.3501666666666665 | 1.4391666666666667 | 3.591833333333333 | 3.9655
5.872333333333334 | 1.4931666666666668 | 3.2435 | 3.9991666666666665
7.481 | 2.263 | 3.3036666666666665 | 3.95
8.818333333333333 | 3.0765 | 3.3063333333333333 | 3.9656666666666665
10.180833333333334 | 4.2525 | 4.4995 | 3.6373333333333333
11.4215 | 5.3345 | 4.814166666666667 | 3.6046666666666667
12.4075 | 5.960333333333334 | 4.741 | 3.4593333333333334
13.315833333333334 | 6.243333333333333 | 4.5925 | 3.3465
14.1625 | 6.450833333333334 | 4.459666666666666 | 2.9245
15.118666666666666 | 6.759333333333333 | 4.6225 | 2.7525
15.984333333333334 | 6.765666666666666 | 4.951833333333333 | 2.556
16.745 | 6.895333333333333 | 4.860333333333333 | 2.291166666666667
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

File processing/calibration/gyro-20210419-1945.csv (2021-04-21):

temperature | x | y | z
-9.0085 | -5.387666666666667 | 2.8906666666666667 | 3.151
-6.6946666666666665 | -3.362833333333333 | 3.079 | 3.4793333333333334
-4.570833333333334 | -0.4081666666666667 | 3.708666666666667 | 3.8385
-2.4386666666666668 | 2.3543333333333334 | 4.4655 | 3.824
-0.428 | 5.1945 | 5.845166666666667 | 4.655833333333334
1.4608333333333334 | 8.362833333333333 | 6.603666666666666 | 4.9215
3.2973333333333334 | 8.156 | 5.484666666666667 | 7.4765
5.079666666666666 | 9.145333333333333 | 5.371833333333333 | 7.752
6.558833333333333 | 10.610666666666667 | 5.754666666666667 | 7.824
8.217833333333333 | 12.599166666666667 | 6.313833333333333 | 7.840166666666667
9.524666666666667 | 13.867166666666666 | 6.316666666666666 | 8.083333333333334
10.754333333333333 | 14.512166666666667 | 6.607666666666667 | 7.958666666666667
11.971833333333333 | 15.4335 | 6.795333333333334 | 7.848833333333333
12.959666666666667 | 16.871 | 7.174833333333333 | 7.7275
13.900333333333334 | 16.977833333333333 | 7.2085 | 7.302666666666667
14.786166666666666 | 15.355166666666667 | 6.623666666666667 | 7.059333333333333
15.7665 | 13.207 | 6.1375 | 6.195
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

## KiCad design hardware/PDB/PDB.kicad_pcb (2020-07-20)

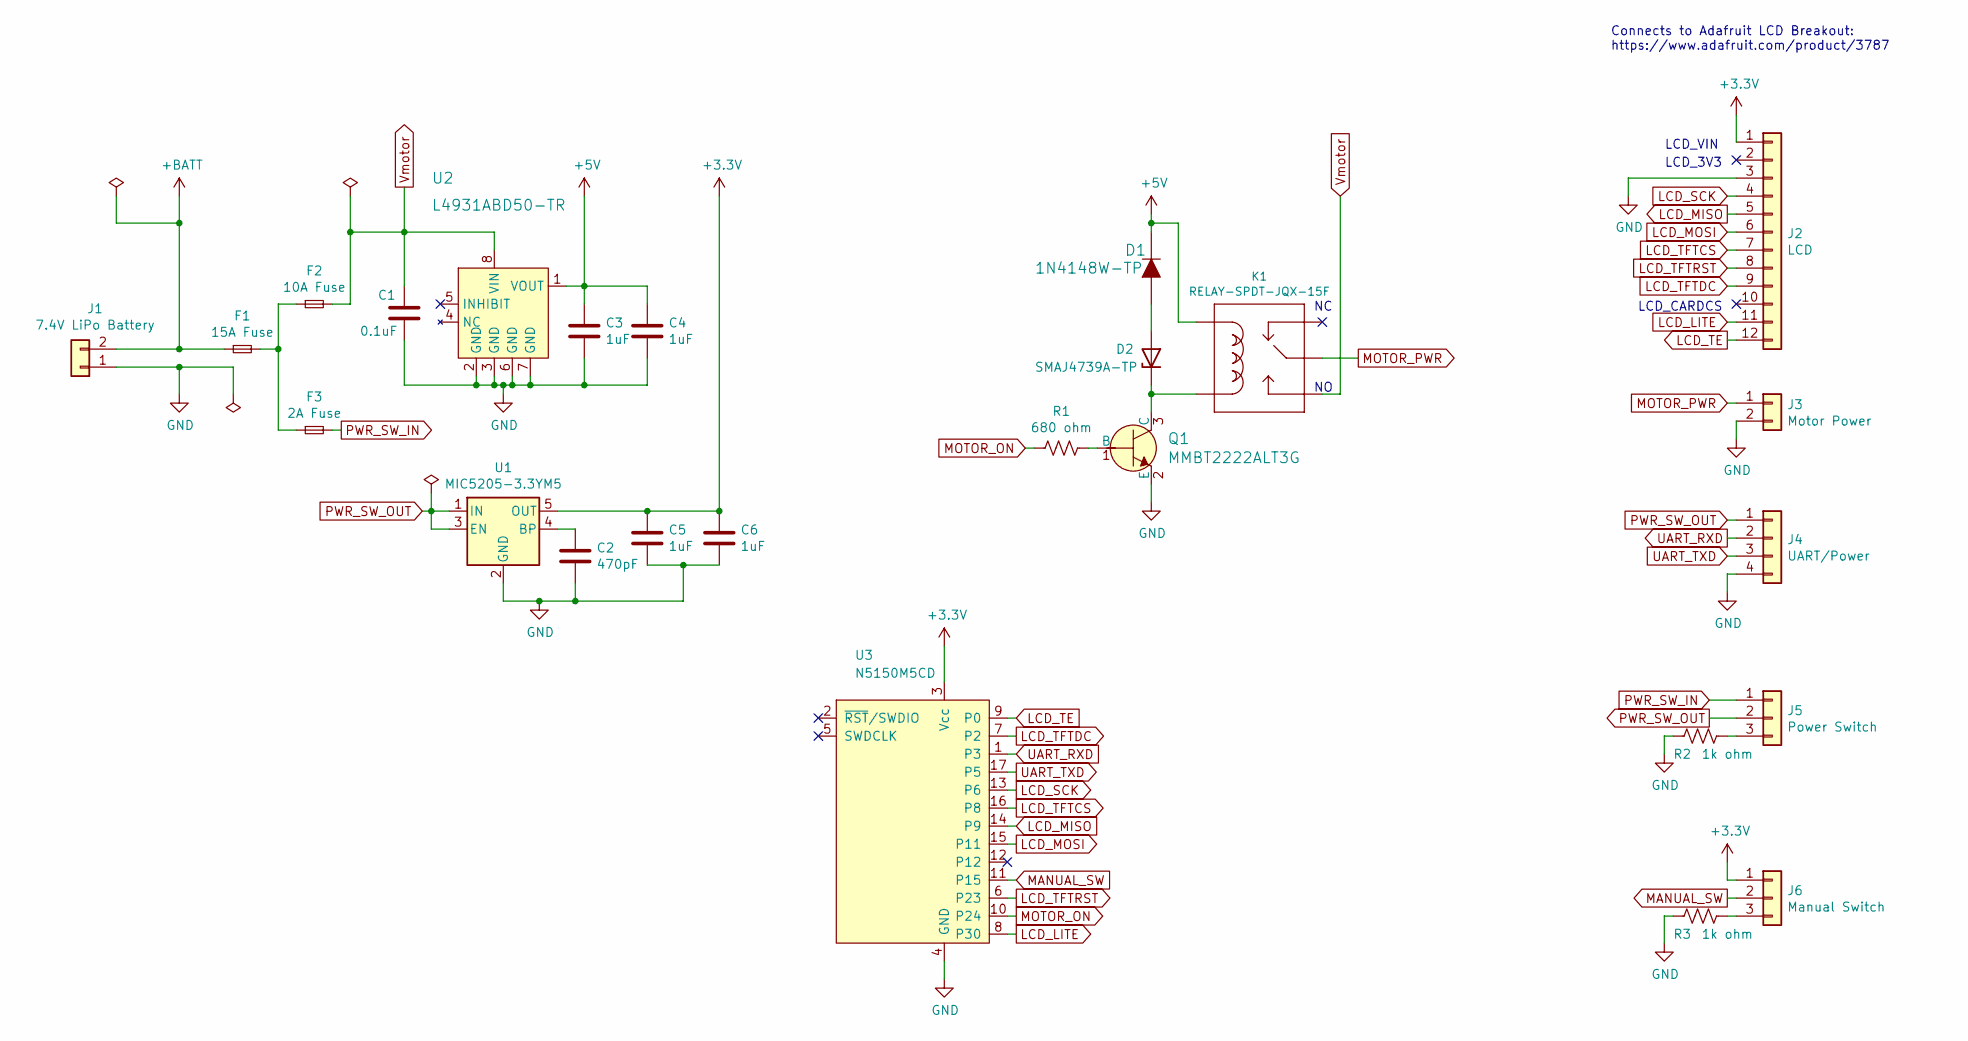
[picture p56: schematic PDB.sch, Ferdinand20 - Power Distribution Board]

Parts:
C1: 0.1uF; C_0805_2012Metric
C2: 470pF; C_0805_2012Metric
C3, C4, C5, C6: 1uF; C_0805_2012Metric
D1: 1N4148W-TP; SOD-123; MPN 1N4148W-TP; Digi-Key_PN 1N4148WTPMSCT-ND
D2: SMAJ4739A-TP; D_SMA
F1: 15A Fuse; SMD_Keystone_Fuse
F2: 10A Fuse; SMD_Keystone_Fuse
F3: 2A Fuse; SMD_Keystone_Fuse
J1: 7.4V LiPo Battery; TerminalBlock_bornier-2_P5.08mm
J2: LCD; PinHeader_1x12_P2.54mm_Vertical
J3: Motor Power; TerminalBlock_bornier-2_P5.08mm
J4: UART/Power; Molex_SPOX_5267-04A_1x04_P2.50mm_Vertical
J5: Power Switch; Molex_SPOX_5267-03A_1x03_P2.50mm_Vertical
J6: Manual Switch; Molex_SPOX_5267-03A_1x03_P2.50mm_Vertical
K1: RELAY-SPDT-JQX-15F; SparkFun-Electromechanical-RELAY-T90
Q1: MMBT2222ALT3G; SOT-23-3; MPN MMBT2222ALT3G; Digi-Key_PN MMBT2222ALT3GOSCT-ND
R1: 680 ohm; R_0805_2012Metric
R2, R3: 1k ohm; R_0805_2012Metric
U1: MIC5205-3.3YM5; SOT-23-5_HandSoldering
U2: L4931ABD50-TR; SOIC-8_W3.9mm; MPN L4931ABD50-TR; Digi-Key_PN 497-1156-1-ND
U3: N5150M5CD; adam_custom-N5150M4CD_TOP

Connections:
+3V3: C5.1, C6.1, J2.1, J6.1, U1.5 (OUT), U3.3 (Vcc)
+5V: C3.1, C4.1, D1.K, K1.COIL1, U2.1 (VOUT)
+BATT: F1.1, J1.2
GND: C1.2, C2.2, C3.2, C4.2, C5.2, C6.2, J1.1, J2.3, J3.2, J4.4, Q1.2 (E), R2.2, R3.2, U1.2 (GND), U2.2 (GND), U2.3 (GND), U2.6 (GND), U2.7 (GND), U3.4 (GND)
LCD_LITE: J2.11, U3.8 (P30)
LCD_MISO: J2.5, U3.14 (P9)
LCD_MOSI: J2.6, U3.15 (P11)
LCD_SCK: J2.4, U3.13 (P6)
LCD_TE: J2.12, U3.9 (P0)
LCD_TFTCS: J2.7, U3.16 (P8)
LCD_TFTDC: J2.9, U3.7 (P2)
LCD_TFTRST: J2.8, U3.6 (P23)
MANUAL_SW: J6.2, U3.11 (P15)
MOTOR_ON: R1.2, U3.10 (P24)
MOTOR_PWR: J3.1, K1.MAIN
unnamed: C2.1, U1.4 (BP)
unnamed: D1.A, D2.2 (A)
unnamed: D2.1 (K), K1.COIL2, Q1.3 (C)
unnamed: F1.2, F2.1, F3.1
unnamed: J5.3, R2.1
unnamed: J6.3, R3.1
unnamed: Q1.1 (B), R1.1
PWR_SW_IN: F3.2, J5.1
PWR_SW_OUT: J4.1, J5.2, U1.1 (IN), U1.3 (EN)
UART_RXD: J4.2, U3.1 (P3)
UART_TXD: J4.3, U3.17 (P5)
Vmotor: C1.1, F2.2, K1.NO, U2.8 (VIN)

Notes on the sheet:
LCD_CARDCS
LCD_3V3
LCD_VIN
Connects to Adafruit LCD Breakout: https://www.adafruit.com/product/3787

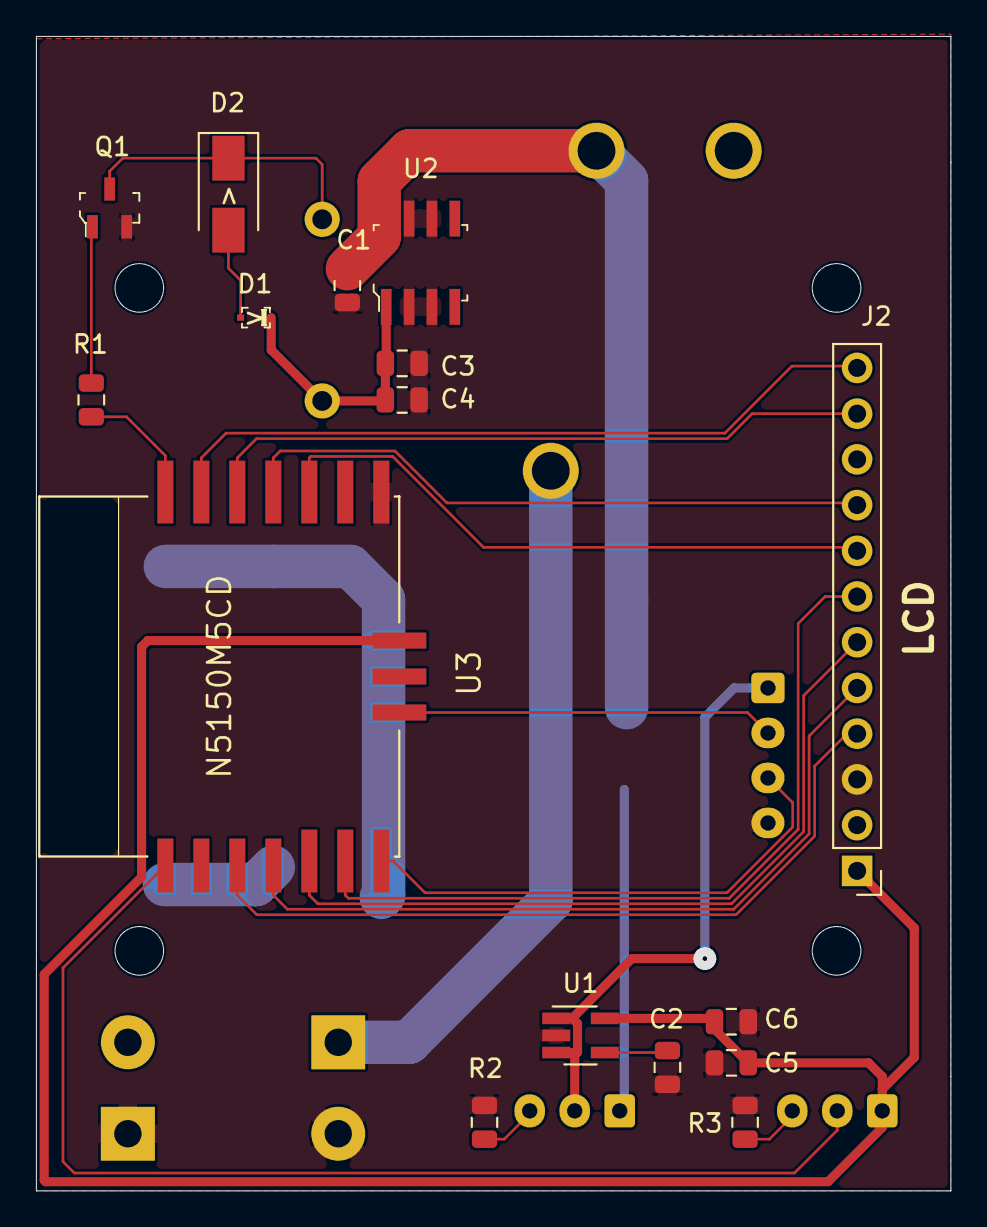
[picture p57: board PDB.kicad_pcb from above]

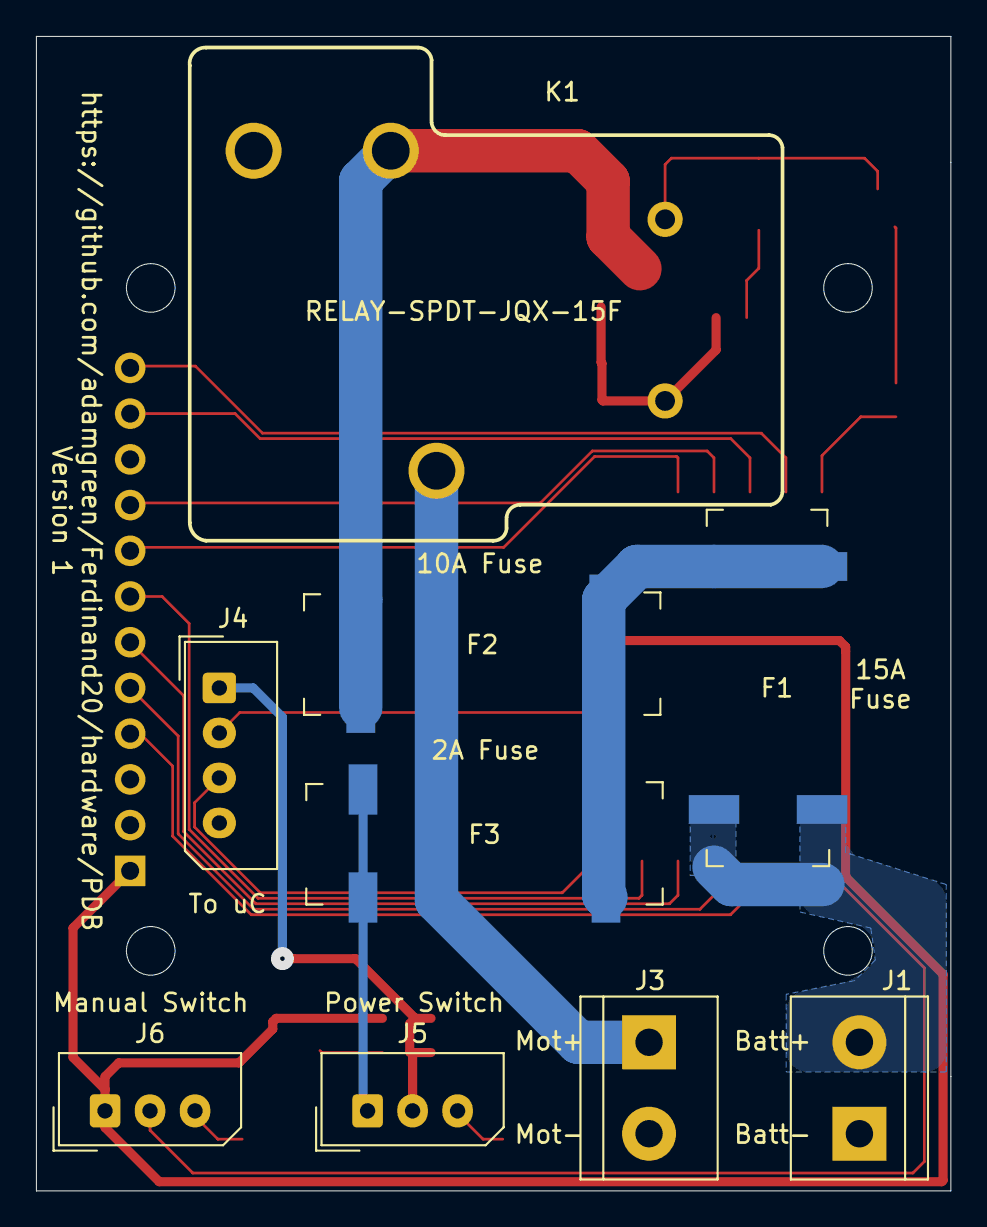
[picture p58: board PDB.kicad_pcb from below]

Board: 2 copper layers, 50.8 x 64.1 mm, 25 parts (9 on the bottom side), 27 nets.

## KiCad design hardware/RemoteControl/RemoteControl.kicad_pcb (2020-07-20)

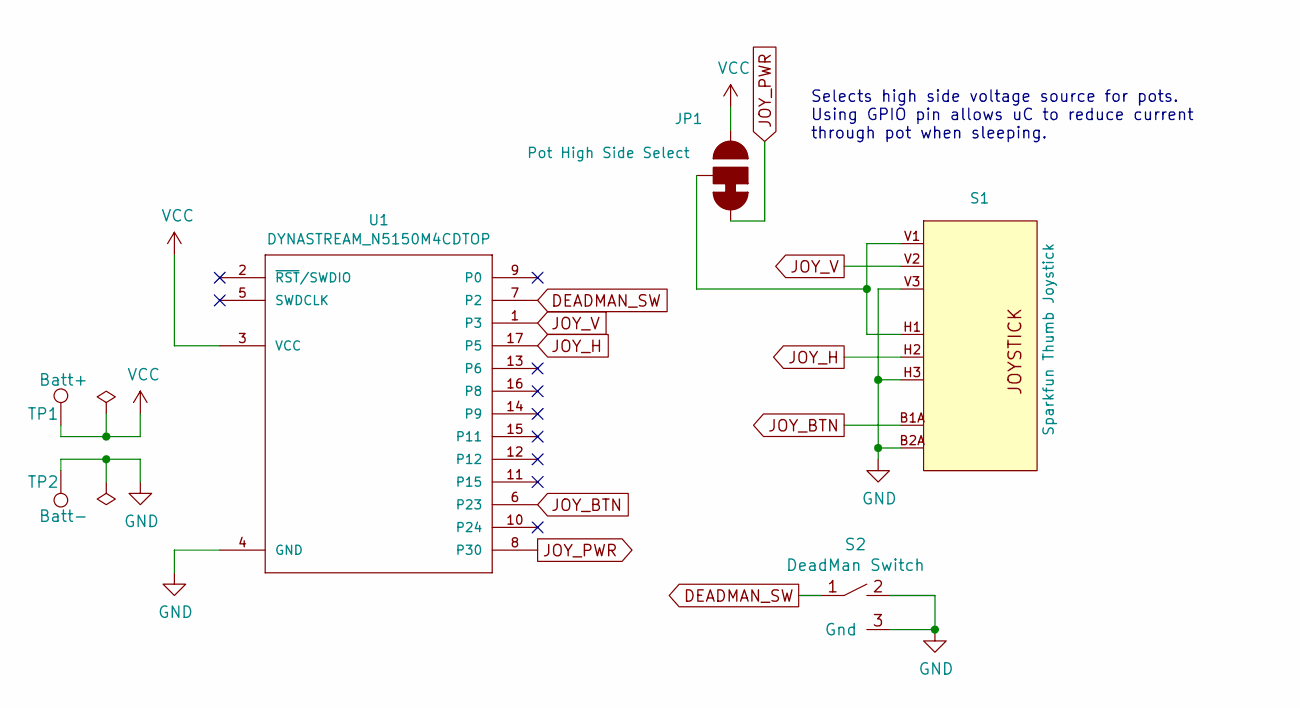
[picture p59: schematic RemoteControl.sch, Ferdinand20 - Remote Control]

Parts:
JP1: Pot High Side Select; SMT-JUMPER_3_1-NC_TRACE_SILK
S1: Sparkfun Thumb Joystick; JOYSTICK
S2: DeadMan Switch; PTS645V-SPST-RightAngleSwitch
TP1: Batt+; TestPoint_Pad_D2.0mm
TP2: Batt-; TestPoint_Pad_D2.0mm
U1: DYNASTREAM_N5150M4CDTOP; adam_custom-N5150M4CD_TOP

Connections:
DEADMAN_SW: S2.1, U1.7 (P2)
GND: S1.B2A (SEL-), S1.H3 (H-), S1.V3 (V-), S2.2, S2.3 (Gnd), TP2.1, U1.4 (GND)
JOY_BTN: S1.B1A (SEL+), U1.6 (P23)
JOY_H: S1.H2 (H), U1.17 (P5)
JOY_PWR: JP1.3, U1.8 (P30)
JOY_V: S1.V2 (V), U1.1 (P3)
unnamed: JP1.2, S1.H1 (H+), S1.V1 (V+)
VCC: JP1.1, TP1.1, U1.3 (VCC)

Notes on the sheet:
Selects high side voltage source for pots. Using GPIO pin allows uC to reduce current through pot when sleeping.

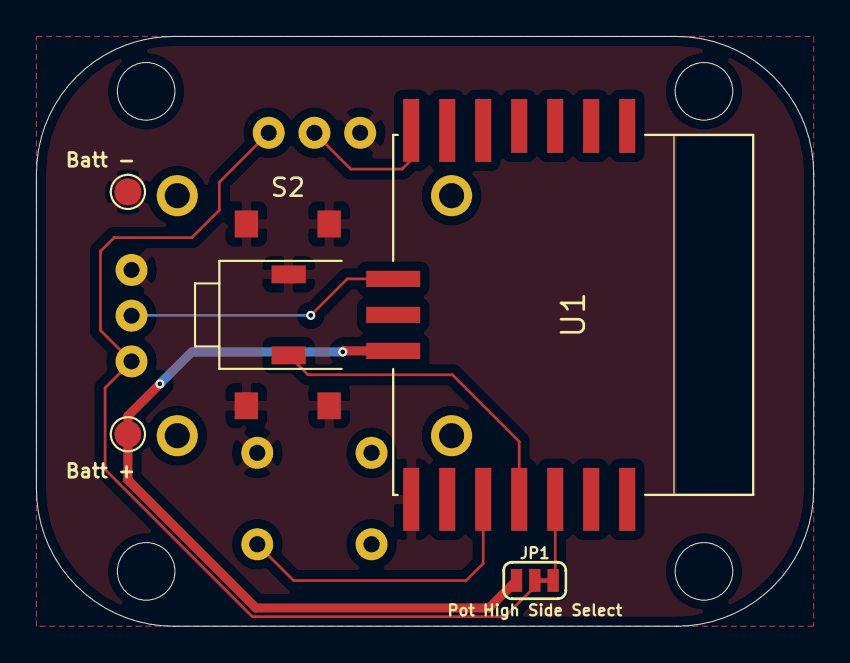
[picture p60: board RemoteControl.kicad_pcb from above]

Board: 2 copper layers, 43.2 x 32.8 mm, 6 parts (1 on the bottom side), 8 nets.

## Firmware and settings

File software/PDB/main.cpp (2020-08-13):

/*  Copyright (C) 2020  Adam Green (https://github.com/adamgreen)

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
    This program is distributed in the hope that it will be useful,
    but WITHOUT ANY WARRANTY; without even the implied warranty of
    MERCHANTABILITY or FITNESS FOR A PARTICULAR PURPOSE.  See the
    GNU General Public License for more details.
*/
/* The firmware for the Ferdinand20 Power Distribution Board. This board performs multiple duties:
   * Controls a relay that switches the robot's motor supply voltage on and off.
   * Only enables the motor supply voltage if a wireless BLE deadman switch is enaged.
   * Monitors the LiPo battery voltage and switches the motor supply relay off if undervoltage is detected.
   * Provides option to allow the user to take manual control with wireless BLE joystick in non-competition
     scenarios. A switch is provided on the PDB to enable this mode.
   * UART connectivity to the robot's main microcontroller
     * Sends battery voltages, joystick and deadman switch state from PDB to robot's main microcontroller.
     * Receives status text to be displayed on screen from robot's main microcontroller.
   * Updates the onboard LCD display with:
     * LiPo battery voltage
     * Wireless BLE remote battery voltage
     * Manual/Auto mode
     * Motor relay on/off state
     * Status messages sent from robot's main microcontroller.

   The hardware pin connections are:
   nRF51 Pin Number     Pin Name            Pin Description
    3                   RX_PIN_NUMBER       UART Receive Input
    5                   TX_PIN_NUMBER       UART Transmit Output
    24                  MOTOR_RELAY_PIN     Relay Enable Output (Pulls ground down to Gnd via NPN transistor)
    15                  MANUAL_SWITCH_PIN   Manual Switch Input (Pulled low when user flips manual switch on)
    12                  LCD_SCK_PIN         LCD SPI Clock Output
    11                  LCD_MOSI_PIN        LCD SPI MOSI Output
    2                   LCD_TFTDC_PIN       LCD Data/Command Output
    8                   LCD_TFTCS_PIN       LCD SPI Chip Select Output
    23                  LCD_TFTRST_PIN      LCD Reset Output
    6 (AIN7)            BATTERY_VOLTAGE_PIN LiPo Battery Voltage Analog Input (via 300/600 ohm voltage divider)

   This sample is heavily influenced by Nordic's BLE UART Service Client (ble_app_uart_c) SDK sample.
*/
#include <stdio.h>
#include <app_uart.h>
#include <app_scheduler.h>
#include <app_timer_appsh.h>
#include <ble.h>
#include <ble_advdata.h>
#include <ble_db_discovery.h>
#include <ble_gap.h>
#include <ble_hci.h>
#include <ble_nus_c.h>
#include <softdevice_handler.h>
#include <nrf_adc.h>
#include <nrf_delay.h>
#include <nrf_gpio.h>
#include <nrf_drv_wdt.h>
#include "../include/BleJoyShared.h"
#include "../include/PdbPacket.h"
#include "Screen.h"


// The UART pins.
#define RX_PIN_NUMBER           3
#define TX_PIN_NUMBER           5

// The output pin used to turn control the motor power relay.
#define MOTOR_RELAY_PIN         24

// The input pin used to read the state of the manual override switch.
#define MANUAL_SWITCH_PIN       15

// The pins used to communicate with the LCD.
#define LCD_SCK_PIN             12
#define LCD_MOSI_PIN            11
#define LCD_TFTDC_PIN           2
#define LCD_TFTCS_PIN           8
#define LCD_TFTRST_PIN          23

// The analog input pin used to read the current LiPo battery voltage through 1/3 voltage divider.
#define BATTERY_VOLTAGE_PIN     NRF_ADC_CONFIG_INPUT_7  // P0.06 is AIN7 on nRF51422.

// The resistors used in battery voltage divider.
#define BATTERY_VOLTAGE_DIVIDER_BOTTOM  327
#define BATTERY_VOLTAGE_DIVIDER_TOP     681
#define BATTERY_VOLTAGE_DIVIDER_TOTAL   (BATTERY_VOLTAGE_DIVIDER_BOTTOM + BATTERY_VOLTAGE_DIVIDER_TOP)

// Low frequency clock source to be used by the SoftDevice
#define NRF_CLOCK_LFCLKSRC      {.source        = NRF_CLOCK_LF_SRC_XTAL,           \
                                 .rc_ctiv       = 0,                              \
                                 .rc_temp_ctiv  = 0,                                \
                                 .xtal_accuracy = NRF_CLOCK_LF_XTAL_ACCURACY_50_PPM}

// Motors will be disabled once the 2S LiPo battery reaches this voltage to protect the battery from under voltage.
//  64 = 6.4V
#define ROBOT_LOW_BATTERY       64

// The LCD update timer must feed the watchdog in this time interval (msec) or the PDB will be reset.
#define WATCHDOG_TIMEOUT        250

// This firmware acts as a BLE central with a single link to the BleJoystick peripheral.
#define CENTRAL_LINK_COUNT      1
// This application doesn't need to act as a BLE peripheral.
#define PERIPHERAL_LINK_COUNT   0

// MTU size used in the softdevice enabling and to reply to a BLE_GATTS_EVT_EXCHANGE_MTU_REQUEST event.
#if (NRF_SD_BLE_API_VERSION == 3)
#define NRF_BLE_MAX_MTU_SIZE    GATT_MTU_SIZE_DEFAULT
#endif

// The size of the transmit and receive arrays for buffering the UART data to and from the main robot uC.
#define UART_TX_BUF_SIZE        256
#define UART_RX_BUF_SIZE        1

// Value of the RTC1 PRESCALER register used by application timer.
#define APP_TIMER_PRESCALER     0
// Size of timer operation queues.
#define APP_TIMER_OP_QUEUE_SIZE 2

// Parameters for configuring how this application scans for nearby BleJoystick peripherals.
// Scan interval between 0x0004 and 0x4000 in 0.625ms units (2.5ms to 10.24s). 0xA0 is equal to 100 milliseconds.
// The central device will switch between advertising channels at this period.
#define SCAN_INTERVAL           0x00A0
// Scan window between 0x0004 and 0x4000 in 0.625ms units (2.5ms to 10.24s). 0x50 is equal to 50 milliseconds.
// The central device will actively scan a single advertising channel for this amount of time.
// Must be <= SCAN_INTERVAL. No scanning is performed for (SCAN_INTERVAL - SCAN_WINDOW) amount of time.
#define SCAN_WINDOW             0x0050
// Timeout when scanning between 0x0001 and 0xFFFF in seconds. 0 disables the timeout so that it keeps scanning as long
// as it is powered up.
#define SCAN_TIMEOUT            0x0000
// If 1, performs active scanning, meaning that it will send scan requests to each advertising device to learn more
// about it.
#define SCAN_ACTIVE             1
// If 1, ignore unknown devices (those not in the whitelist).
#define SCAN_SELECTIVE          0

// If the lcdTimeoutHandler() routine doesn't see new BLE JoyData packets for this many iterations then it considers
// the remote control to have been disconnected.
#define MAX_MISSED_BLE_PACKETS  30

// Timings for how often peripheral and central should communicate over the link. The shorter the interval, the more
// data that can be sent over the link but uses more CPU and power resources.
// Minimum acceptable connection interval in milliseconds. Connection interval uses 1.25 ms units.
#define MIN_CONNECTION_INTERVAL MSEC_TO_UNITS(8, UNIT_1_25_MS)
// Maximum acceptable connection interval in milliseconds. Connection interval uses 1.25 ms units.
#define MAX_CONNECTION_INTERVAL MSEC_TO_UNITS(16, UNIT_1_25_MS)
// The number of the connection interval events that the peripheral can ignore before response is required.
#define SLAVE_LATENCY           0
// Connection supervisory timeout (4 seconds), Supervision Timeout uses 10 ms units.
#define SUPERVISION_TIMEOUT     MSEC_TO_UNITS(4000, UNIT_10_MS)

// The size in bytes of the various UUID bit-sized types.
#define UUID16_SIZE             (16/8)
#define UUID32_SIZE             (32/8)
#define UUID128_SIZE            (128/8)

// Maximum size of scheduled events - Only timer events are placed in this queue.
#define SCHED_MAX_EVENT_DATA_SIZE       APP_TIMER_SCHED_EVT_SIZE
// Maximum number of events to be schedule at once.
#define SCHED_QUEUE_SIZE                2

// The delay to be used between LCD/UART updates.
#define LCD_TIMER_DELAY         APP_TIMER_TICKS(16, APP_TIMER_PRESCALER)
// The number of ticks in a second.
#define TICKS_PER_SECOND        APP_TIMER_TICKS(1000, APP_TIMER_PRESCALER)
//Interval to be used between battery voltage level measurements.
#define BATTERY_TIMER_INTERVAL  APP_TIMER_TICKS((60000), APP_TIMER_PRESCALER)



// Format of full packet when in manual driving mode. Contains header and joystick info.
struct ManualPacket
{
    PdbSerialPacketHeader header;
    PdbSerialManualPacket manual;
};

// Format of full packet when in auto mode.
struct AutoPacket
{
    PdbSerialPacketHeader header;
    PdbSerialAutoPacket   _auto;
};

// Circular queue class used for serial data received from robot microcontroller for display on LCD.
template <uint32_t SIZE>
class CircularQueue
{
    public:
        CircularQueue()
        {
            m_pushIndex = 0;
            m_popIndex = 0;
        }

        bool isFull()
        {
            return m_pushIndex + 1 == m_popIndex;
        }

        bool isEmpty()
        {
            return m_pushIndex == m_popIndex;
        }

        uint32_t freeByteCount()
        {
            uint32_t pushIndex = m_pushIndex;
            uint32_t popIndex = m_popIndex;

            if (pushIndex < popIndex)
            {
                return popIndex - pushIndex - 1;
            }
            else
            {
                return (SIZE - 1) - (pushIndex - popIndex);
            }
        }

        void push(uint8_t byte)
        {
            ASSERT ( !isFull() );
            m_data[m_pushIndex] = byte;
            m_pushIndex = nextIndex(m_pushIndex);
        }

        uint8_t pop()
        {
            ASSERT ( !isEmpty() );
            uint8_t byte = m_data[m_popIndex];
            m_popIndex = nextIndex(m_popIndex);
            return byte;
        }


    protected:
        uint32_t nextIndex(uint32_t index)
        {
            return (index + 1) % SIZE;
        }

        volatile uint32_t m_pushIndex;
        volatile uint32_t m_popIndex;
        volatile uint8_t  m_data[SIZE];
};


static ble_nus_c_t              g_nordicUartServiceClient;
static ble_db_discovery_t       g_bleDatabaseDiscovery;

static const ble_gap_conn_params_t g_bleConnectionParameters =
{
    (uint16_t)MIN_CONNECTION_INTERVAL,
    (uint16_t)MAX_CONNECTION_INTERVAL,
    (uint16_t)SLAVE_LATENCY,
    (uint16_t)SUPERVISION_TIMEOUT
};

static const ble_gap_scan_params_t g_bleScanParameters =
{
    .active   = 1,
#if (NRF_SD_BLE_API_VERSION == 2)
    .selective   = SCAN_SELECTIVE,
    .p_whitelist = NULL,
#endif
#if (NRF_SD_BLE_API_VERSION == 3)
    .use_whitelist = SCAN_SELECTIVE,
#endif
    .interval = SCAN_INTERVAL,
    .window   = SCAN_WINDOW,
    .timeout  = SCAN_TIMEOUT,
};

// Only BleJoystick devices reporting this UUID in their advertisement scan data will be connected to.
static const ble_uuid_t g_bleJoystickUuid =
{
    .uuid = BLEJOY_ADVERTISE_UUID,
    .type = BLEJOY_ADVERTISE_UUID_TYPE
};

// Timer object used for updating LCD and sending UART packets.
APP_TIMER_DEF(g_lcdTimer);
// Timer object used for reading the battery voltage.
APP_TIMER_DEF(g_batteryTimer);

// Objects used to control the LCD over SPI.
static Screen  g_screen(TICKS_PER_SECOND, LCD_MOSI_PIN, LCD_SCK_PIN, LCD_TFTCS_PIN, LCD_TFTDC_PIN, LCD_TFTRST_PIN);

// This global is set if the robot's LiPo battery drops below the minimum allowed voltage.
// Once set, the motors can no longer be enabled with the deadman switch without power cycling the PDB.
static volatile bool g_isBatteryTooLow = false;

// Global object used to track the PDB state. Used for updating the LCD.
static Screen::PdbState g_state =
{
    .isManualMode = false,
    .isRemoteConnected = false,
    .areMotorsEnabled = false,
    .robotBattery = 0,
    .remoteBattery = 0
};

// Global object used to record the most recent joystick state returned from remote control.
static BleJoyData   g_joyData;

// Count of BLE packets that have been received from the remote control.
static volatile uint32_t    g_blePacketCount = 0;

// The last count seen in g_blePacketCount by lcdTimeoutHandler().
static uint32_t             g_lastBlePacketCount = 0;

// The number of times lcdTimeoutHandler() has seen no new BLE packets.
static uint32_t             g_missingBlePacketCount = 0;

// The packet sent when in manual driving mode.
static ManualPacket g_manualPacket =
{
    .header =
    {
        .signature = PDBSERIAL_PACKET_SIGNATURE,
        .length = sizeof(PdbSerialManualPacket)
    },
    .manual = {
        .x = 0,
        .y = 0,
        .robotBattery = 0,
        .remoteBattery = 0,
        .flags = 0
    }
};

// The packet sent when in auto driving mode.
static AutoPacket g_autoPacket =
{
    .header =
    {
        .signature = PDBSERIAL_PACKET_SIGNATURE,
        .length = sizeof(PdbSerialAutoPacket)
    },
    ._auto = {
        .robotBattery = 0,
        .remoteBattery = 0,
        .flags = 0
    }
};

// The states that the code can be in when parsing UART data sent back from the main robot microcontroller.
static enum UartRecvState
{
    UART_RECV_PACKET_START,
    UART_RECV_PACKET_LENGTH,
    UART_RECV_PACKET_DATA,
    UART_RECV_IGNORE_DATA
} g_recvPacketState = UART_RECV_PACKET_START;

// Number of received packets that had to be dropped because of queue overflow.
static uint32_t g_recvPacketIgnoredCount = 0;

// Number of currently available packets to be pulled from queue.
static volatile uint32_t g_recvPacketQueueCount = 0;

// Length of packet data currently being placed in queue or being dropped.
static uint32_t g_recvPacketLength = 0;

// Progress of transferring packet data into queue or being dropped.
static uint32_t g_recvPacketIndex = 0;

// Circular queue used for serial data received from robot microcontroller for display on LCD.
static CircularQueue<256> g_recvPacketQueue;

// Watchdog channel to be fed by lcdTimeoutHandler().
static nrf_drv_wdt_channel_id g_watchdogChannel;



// Function Prototypes
static void initTimers(void);
static void lcdTimeoutHandler(void* pvContext);
static void checkForMissingBlePackets(Screen::PdbState* pState, BleJoyData* pJoyData);
static void sendSerialPacket(const Screen::PdbState* pState, const BleJoyData* pJoyData);
static void sendBufferToUart(const void* pvData, size_t length);
static uint32_t interlockedDecrement(volatile uint32_t* pVal);
static void startLcdTimer(void);
static void batteryTimeoutHandler(void* pvContext);
static void readBatteryVoltage(void);
static void initUart(void);
static void uartEventHandler(app_uart_evt_t* pEvent);
static void parseReceivedPacketByte(uint8_t byte);
static uint32_t interlockedIncrement(volatile uint32_t* pVal);
static void initButtonsAndLeds(void);
static void initBatteryVoltageReading(void);
static void initDatabaseDiscoveryModule(void);
static void databaseDiscoveryEventHandler(ble_db_discovery_evt_t* pEvent);
static void initBleStack(void);
static void bleEventDispatcher(ble_evt_t* pBleEvent);
static void bleEventHandler(ble_evt_t * pBleEvent);
static bool isUuidPresent(const ble_uuid_t* pTargetUuid, const ble_gap_evt_adv_report_t* pAdvertiseReport);
static void initNordicUartServiceClient(void);
static void nordicUartServiceClientEventHandler(ble_nus_c_t* pNordicUartServiceClient, const ble_nus_c_evt_t* pEvent);
static void startWatchdog(void);
static void watchdogTimeoutHandler(void);
static void startBatteryTimer(void);
static void startScanningForNordicUartPeripherals(void);
static void enterLowPowerModeUntilNextEvent(void);



int main(void)
{
    APP_SCHED_INIT(SCHED_MAX_EVENT_DATA_SIZE, SCHED_QUEUE_SIZE);
    initTimers();

    initUart();
    initButtonsAndLeds();
    initBatteryVoltageReading();

    initDatabaseDiscoveryModule();
    initBleStack();
    initNordicUartServiceClient();

    startWatchdog();
    startLcdTimer();
    startBatteryTimer();
    startScanningForNordicUartPeripherals();

    for (;;)
    {
        enterLowPowerModeUntilNextEvent();
    }
}


static void initTimers(void)
{
    // Initialize timer module, making it use the scheduler.
    APP_TIMER_APPSH_INIT(APP_TIMER_PRESCALER, APP_TIMER_OP_QUEUE_SIZE, true);

    // Create LCD and UART update timer.
    uint32_t errorCode = app_timer_create(&g_lcdTimer, APP_TIMER_MODE_SINGLE_SHOT, lcdTimeoutHandler);
    APP_ERROR_CHECK(errorCode);

    // Create battery voltage sampling timer.
    errorCode = app_timer_create(&g_batteryTimer, APP_TIMER_MODE_REPEATED, batteryTimeoutHandler);
    APP_ERROR_CHECK(errorCode);
}

static void lcdTimeoutHandler(void* pvContext)
{
    // Take a snapshot of the remote and PDB state as they exist at the beginning of this timer. That way one part of
    // this handler doesn't see a different state than another part.
    Screen::PdbState state = g_state;
    BleJoyData       joyData = g_joyData;

    // Mark remote as not being connected if we haven't received any packets from it for a few iterations of this
    // callback.
    checkForMissingBlePackets(&state, &joyData);

    // Make sure that motors get disabled once the LiPo battery voltage gets too low.
    if (g_isBatteryTooLow)
    {
        joyData.buttons &= ~BLEJOY_BUTTONS_DEADMAN;
    }

    // Set motor relay enable pin based on latest remote dead man switch state just received.
    nrf_gpio_pin_write(MOTOR_RELAY_PIN, joyData.buttons & BLEJOY_BUTTONS_DEADMAN);

    // Read the state of the manual override switch.
    uint32_t manualButtonPressed = nrf_gpio_pin_read(MANUAL_SWITCH_PIN);
    state.isManualMode = (manualButtonPressed == 1);

    // Set PDB state fields from most recent joystick data.
    state.remoteBattery = joyData.batteryVoltage;
    state.areMotorsEnabled = joyData.buttons & BLEJOY_BUTTONS_DEADMAN;

    g_screen.update(&state);
    if (g_recvPacketQueueCount > 0)
    {
        char buffer[Screen::TEXT_LINE_LENGTH + 1];
        char* pBuffer = buffer;

        uint8_t textLength = g_recvPacketQueue.pop();
        for (uint8_t i = 0 ; i < textLength ; i++)
        {
            uint8_t byte = g_recvPacketQueue.pop();
            if (i < sizeof(buffer) - 1)
            {
                *pBuffer++ = byte;
            }
        }
        *pBuffer = '\0';
        g_screen.updateText(buffer);
        interlockedDecrement(&g_recvPacketQueueCount);
    }

    // Send serial packet to robot microcontroller.
    sendSerialPacket(&state, &joyData);

    // Feed the watchdog timer.
    nrf_drv_wdt_channel_feed(g_watchdogChannel);

    // Restart the timer again.
    startLcdTimer();
}

static void checkForMissingBlePackets(Screen::PdbState* pState, BleJoyData* pJoyData)
{
    if (g_blePacketCount == g_lastBlePacketCount)
    {
        // No new BLE packets from the remote control since the last time this function ran.
        g_missingBlePacketCount++;
        if (g_missingBlePacketCount > MAX_MISSED_BLE_PACKETS)
        {
            // Not receiving BLE packets from remote control so force deadman switch status to unpressed state.
            pJoyData->buttons &= ~BLEJOY_BUTTONS_DEADMAN;
            pState->isRemoteConnected = false;
        }
    }
    else
    {
        // Remember that we have seen this latest BLE packet.
        g_lastBlePacketCount = g_blePacketCount;
        g_missingBlePacketCount = 0;
    }

}

static void sendSerialPacket(const Screen::PdbState* pState, const BleJoyData* pJoyData)
{
    if (pState->isManualMode)
    {
        g_manualPacket.manual.x = pJoyData->x;
        g_manualPacket.manual.y = pJoyData->y;
        g_manualPacket.manual.robotBattery = pState->robotBattery;
        g_manualPacket.manual.remoteBattery = pState->remoteBattery;
        g_manualPacket.manual.flags = ((pJoyData->buttons & BLEJOY_BUTTONS_JOYSTICK) ? PDBSERIAL_FLAGS_JOYSTICK_BUTTON : 0) |
                                      (pState->areMotorsEnabled ? PDBSERIAL_FLAGS_MOTORS_ENABLED : 0) |
                                      (pState->isRemoteConnected ? PDBSERIAL_FLAGS_REMOTE_CONNECTED : 0);
        sendBufferToUart(&g_manualPacket, sizeof(g_manualPacket));
    }
    else
    {
        g_autoPacket._auto.robotBattery = pState->robotBattery;
        g_autoPacket._auto.remoteBattery = pState->remoteBattery;
        g_autoPacket._auto.flags = (pState->areMotorsEnabled ? PDBSERIAL_FLAGS_MOTORS_ENABLED : 0) |
                                   (pState->isRemoteConnected ? PDBSERIAL_FLAGS_REMOTE_CONNECTED : 0);
        sendBufferToUart(&g_autoPacket, sizeof(g_autoPacket));
    }
}

static void sendBufferToUart(const void* pvData, size_t length)
{
    const uint8_t* pData = (const uint8_t*)pvData;
    while (length-- > 0)
    {
        uint32_t errorCode = app_uart_put(*pData++);
        APP_ERROR_CHECK(errorCode);
    }
}

static uint32_t interlockedDecrement(volatile uint32_t* pVal)
{
    uint32_t newValue;
    CRITICAL_REGION_ENTER();
        newValue = *pVal - 1;
        *pVal = newValue;
    CRITICAL_REGION_EXIT();
    return newValue;
}

static void startLcdTimer(void)
{
    // Start the timer used to send UART packets and update LCD at regular intervals.
    uint32_t errorCode = app_timer_start(g_lcdTimer, LCD_TIMER_DELAY, NULL);
    APP_ERROR_CHECK(errorCode);
}

static void batteryTimeoutHandler(void* pvContext)
{
    // Process the most recent battery voltage ADC conversion if ready.
    if (nrf_adc_conversion_finished())
    {
        readBatteryVoltage();
    }
}

static void readBatteryVoltage(void)
{
    // Read the last ADC battery voltage read.
    uint32_t adcReading = nrf_adc_result_get();

    // Convert to 10 X Volts.
    g_state.robotBattery = adcReading * 36 * BATTERY_VOLTAGE_DIVIDER_TOTAL / (1023 * BATTERY_VOLTAGE_DIVIDER_BOTTOM);

    // Set global flag if the battery level ever gets too low so that motors can be disabled to protect the battery.
    if (g_state.robotBattery <= ROBOT_LOW_BATTERY)
    {
        g_isBatteryTooLow = true;
    }

    // Start the next conversion.
    nrf_adc_conversion_event_clean();
    nrf_adc_start();
}
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

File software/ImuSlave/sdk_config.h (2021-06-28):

#ifndef SDK_CONFIG_H
#define SDK_CONFIG_H
// <<< Use Configuration Wizard in Context Menu >>>\n
#ifdef USE_APP_CONFIG
#include "app_config.h"
#endif
// <h> Application

// <e> TWI_ENABLED - nrf_drv_twi - TWI/TWIM peripheral driver
//==========================================================
#ifndef TWI_ENABLED
#define TWI_ENABLED 1
#endif
#if  TWI_ENABLED
// <o> TWI_DEFAULT_CONFIG_FREQUENCY  - Frequency

// <26738688=> 100k
// <67108864=> 250k
// <104857600=> 400k

#ifndef TWI_DEFAULT_CONFIG_FREQUENCY
#define TWI_DEFAULT_CONFIG_FREQUENCY 26738688
#endif

// <q> TWI_DEFAULT_CONFIG_CLR_BUS_INIT  - Enables bus clearing procedure during init


#ifndef TWI_DEFAULT_CONFIG_CLR_BUS_INIT
#define TWI_DEFAULT_CONFIG_CLR_BUS_INIT 0
#endif

// <q> TWI_DEFAULT_CONFIG_HOLD_BUS_UNINIT  - Enables bus holding after uninit


#ifndef TWI_DEFAULT_CONFIG_HOLD_BUS_UNINIT
#define TWI_DEFAULT_CONFIG_HOLD_BUS_UNINIT 0
#endif

// <o> TWI_DEFAULT_CONFIG_IRQ_PRIORITY  - Interrupt priority


// <i> Priorities 0,2 (nRF51) and 0,1,4,5 (nRF52) are reserved for SoftDevice
// <0=> 0 (highest)
// <1=> 1
// <2=> 2
// <3=> 3
// <4=> 4
// <5=> 5
// <6=> 6
// <7=> 7

#ifndef TWI_DEFAULT_CONFIG_IRQ_PRIORITY
#define TWI_DEFAULT_CONFIG_IRQ_PRIORITY 7
#endif

// <e> TWI0_ENABLED - Enable TWI0 instance
//==========================================================
#ifndef TWI0_ENABLED
#define TWI0_ENABLED 1
#endif
#if  TWI0_ENABLED
// <q> TWI0_USE_EASY_DMA  - Use EasyDMA (if present)


#ifndef TWI0_USE_EASY_DMA
#define TWI0_USE_EASY_DMA 1
#endif

#endif //TWI0_ENABLED
// </e>

// <e> TWI1_ENABLED - Enable TWI1 instance
//==========================================================
#ifndef TWI1_ENABLED
#define TWI1_ENABLED 0
#endif
#if  TWI1_ENABLED
// <q> TWI1_USE_EASY_DMA  - Use EasyDMA (if present)


#ifndef TWI1_USE_EASY_DMA
#define TWI1_USE_EASY_DMA 0
#endif

#endif //TWI1_ENABLED
// </e>

// <e> TWI_CONFIG_LOG_ENABLED - Enables logging in the module.
//==========================================================
#ifndef TWI_CONFIG_LOG_ENABLED
#define TWI_CONFIG_LOG_ENABLED 0
#endif
#if  TWI_CONFIG_LOG_ENABLED
// <o> TWI_CONFIG_LOG_LEVEL  - Default Severity level

// <0=> Off
// <1=> Error
// <2=> Warning
// <3=> Info
// <4=> Debug

#ifndef TWI_CONFIG_LOG_LEVEL
#define TWI_CONFIG_LOG_LEVEL 3
#endif

// <o> TWI_CONFIG_INFO_COLOR  - ANSI escape code prefix.

// <0=> Default
// <1=> Black
// <2=> Red
// <3=> Green
// <4=> Yellow
// <5=> Blue
// <6=> Magenta
// <7=> Cyan
// <8=> White

#ifndef TWI_CONFIG_INFO_COLOR
#define TWI_CONFIG_INFO_COLOR 0
#endif

// <o> TWI_CONFIG_DEBUG_COLOR  - ANSI escape code prefix.

// <0=> Default
// <1=> Black
// <2=> Red
// <3=> Green
// <4=> Yellow
// <5=> Blue
// <6=> Magenta
// <7=> Cyan
// <8=> White

#ifndef TWI_CONFIG_DEBUG_COLOR
#define TWI_CONFIG_DEBUG_COLOR 0
#endif

#endif //TWI_CONFIG_LOG_ENABLED
// </e>

#endif //TWI_ENABLED
// </e>

//==========================================================
// <h> SPIS_CONFIGURATION - Spi slave configuration

//==========================================================
// <o> APP_SPIS_SCK_PIN - Pin number  <0-31>


#ifndef APP_SPIS_SCK_PIN
#define APP_SPIS_SCK_PIN 3
#endif

// <o> APP_SPIS_MISO_PIN - Pin number  <0-31>


#ifndef APP_SPIS_MISO_PIN
#define APP_SPIS_MISO_PIN 28
#endif

// <o> APP_SPIS_MOSI_PIN - Pin number  <0-31>


#ifndef APP_SPIS_MOSI_PIN
#define APP_SPIS_MOSI_PIN 4
#endif

// <o> APP_SPIS_CS_PIN - Pin number  <0-31>


#ifndef APP_SPIS_CS_PIN
#define APP_SPIS_CS_PIN 29
#endif

// <o> APP_SPIS_IRQ_PRIORITY  - Interrupt priority


// <i> Priorities 0,2 (nRF51) and 0,1,4,5 (nRF52) are reserved for SoftDevice
// <0=> 0 (highest)
// <1=> 1
// <2=> 2
// <3=> 3
// <4=> 4
// <5=> 5
// <6=> 6
// <7=> 7

#ifndef APP_SPIS_IRQ_PRIORITY
#define APP_SPIS_IRQ_PRIORITY 7
#endif

// </h>
//==========================================================

// </h>
//==========================================================

// <h> nRF_Drivers

//==========================================================
// <e> GPIOTE_ENABLED - nrf_drv_gpiote - GPIOTE peripheral driver
//==========================================================
#ifndef GPIOTE_ENABLED
#define GPIOTE_ENABLED 1
#endif
#if  GPIOTE_ENABLED
// <o> GPIOTE_CONFIG_NUM_OF_LOW_POWER_EVENTS - Number of lower power input pins
#ifndef GPIOTE_CONFIG_NUM_OF_LOW_POWER_EVENTS
#define GPIOTE_CONFIG_NUM_OF_LOW_POWER_EVENTS 4
#endif

// <o> GPIOTE_CONFIG_IRQ_PRIORITY  - Interrupt priority


// <i> Priorities 0,2 (nRF51) and 0,1,4,5 (nRF52) are reserved for SoftDevice
// <0=> 0 (highest)
// <1=> 1
// <2=> 2
// <3=> 3
// <4=> 4
// <5=> 5
// <6=> 6
// <7=> 7

#ifndef GPIOTE_CONFIG_IRQ_PRIORITY
#define GPIOTE_CONFIG_IRQ_PRIORITY 7
#endif

// <e> GPIOTE_CONFIG_LOG_ENABLED - Enables logging in the module.
//==========================================================
#ifndef GPIOTE_CONFIG_LOG_ENABLED
#define GPIOTE_CONFIG_LOG_ENABLED 0
#endif
#if  GPIOTE_CONFIG_LOG_ENABLED
// <o> GPIOTE_CONFIG_LOG_LEVEL  - Default Severity level
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

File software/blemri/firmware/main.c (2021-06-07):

/*  Copyright (C) 2021  Adam Green (https://github.com/adamgreen)

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
    This program is distributed in the hope that it will be useful,
    but WITHOUT ANY WARRANTY; without even the implied warranty of
    MERCHANTABILITY or FITNESS FOR A PARTICULAR PURPOSE.  See the
    GNU General Public License for more details.
*/
/* A Bluetooth Low Energy (BLE) to UART bridge to be used between the MRI debug monitor and the Macintosh running GDB.

   More information about MRI can be found here: https://github.com/adamgreen/mri
   The Macintosh running GDB also needs to run the macOS portion of BLEMRI to act as a bridge between BLE and the
   TCP/IP protocol since GDB knows how to use TCP/IP but not BLE for remote target debugging.

   Currently the hardware pin connections are:

   nRF51 Pin Number     Pin Name        Pin Description
          1             UART_RX_PIN     Connected to the MRI serial Tx line
          2             UART_TX_PIN     Connected to the MRI serial Rx line

   This sample is heavily influenced by Nordic's BLE UART Service (ble_app_uart) SDK sample.
*/
#include <app_button.h>
#include <app_scheduler.h>
#include <app_simple_timer.h>
#include <app_timer.h>
#include <app_uart.h>
#include <app_util_platform.h>
#include <ble_advdata.h>
#include <ble_advertising.h>
#include <ble_conn_params.h>
#include <ble_hci.h>
#include <ble_nus.h>
#include <bsp.h>
#include <bsp_btn_ble.h>
#include <nordic_common.h>
#include <nrf.h>
#include <softdevice_handler.h>



// UART Pin Connections
#define UART_RX_PIN                     1
#define UART_TX_PIN                     2

// UART Baud Rate
#define UART_BAUD_RATE_NRF_BITMASK      UART_BAUDRATE_BAUDRATE_Baud115200
#define UART_BAUD_RATE                  115200

// If haven't received any more data from UART in this amount of bit times, then send what we have already received.
// 15 is 1.5 UART frames.
#define UART_NAGLE_BIT_TIMES            15
#define UART_NAGLE_TIME_MICROSECONDS    ((UART_NAGLE_BIT_TIMES * 1000000) / 115200)

// The <= 20 byte chunks of UART data to be sent over BLE can be queued up if a BLE_ERROR_NO_TX_PACKETS is
// encountered when attempting the BLE send.
#define SERIAL_CHUNK_QUEUE_SIZE         64

// The maximum number of UART buffers that can be queued up in the app scheduler to be sent from main thread.
#define MAX_SERIAL_BUFFERS              16

// This is the vendor UUID offset to be advertised by BLEMRI devices.
#define BLEMRI_ADVERTISE                BLE_UUID_NUS_SERVICE


// The service database for this device can't be changed at runtime. Must be non-zero for DFU.
#define IS_SRVC_CHANGED_CHARACT_PRESENT 0

#if (NRF_SD_BLE_API_VERSION == 3)
// MTU size used in the softdevice enabling and to reply to a BLE_GATTS_EVT_EXCHANGE_MTU_REQUEST event.
#define NRF_BLE_MAX_MTU_SIZE            GATT_MTU_SIZE_DEFAULT
#endif

// Reply when unsupported features are requested.
#define APP_FEATURE_NOT_SUPPORTED       BLE_GATT_STATUS_ATTERR_APP_BEGIN + 2

// This application doesn't need to act as a central device.
#define CENTRAL_LINK_COUNT              0
// This application is a peripheral and only hosts 1 peripheral link back to a central device.
#define PERIPHERAL_LINK_COUNT           1

#define DEVICE_NAME                     "BLEMRI"

// UUID type for the Nordic UART Service (vendor specific).
#define NUS_SERVICE_UUID_TYPE           BLE_UUID_TYPE_VENDOR_BEGIN

// The advertising interval (in units of 0.625 ms. This value corresponds to 40 ms).
#define APP_ADV_INTERVAL                64
// The advertising timeout (in units of seconds).
#define APP_ADV_TIMEOUT_IN_SECONDS      180

// Value of the RTC1 PRESCALER register.
#define APP_TIMER_PRESCALER             0
// Size of timer operation queues.
#define APP_TIMER_OP_QUEUE_SIZE         4

// Timings for how often peripheral and central should communicate over the link. The shorter the interval, the lower
// the link latency but at the cost of higher power usage.
// Apple's Accessory Design Guidelines places some extra constraints on these parameters:
// * Peripheral Latency of up to 30 connection intervals.
// * Supervision Timeout from 2 seconds to 6 seconds.
// * Interval Min of at least 15 ms.
// * Interval Min is a multiple of 15 ms.
// * One of the following:
//   * Interval Max at least 15 ms greater than Interval Min.
//    * Interval Max and Interval Min both set to 15 ms.
// * Interval Max * (Peripheral Latency + 1) of 2 seconds or less.
// * Supervision Timeout greater than Interval Max * (Peripheral Latency + 1) * 3.
// Minimum acceptable connection interval in ms (7.5 ms is smallest allowed). Connection interval uses 1.25 ms units.
#define MIN_CONN_INTERVAL               MSEC_TO_UNITS(15, UNIT_1_25_MS)
// Maximum acceptable connection interval in ms. Connection interval uses 1.25 ms units.
#define MAX_CONN_INTERVAL               MSEC_TO_UNITS(15, UNIT_1_25_MS)
// The number of the connection interval events that the peripheral can ignore before response is required.
#define SLAVE_LATENCY                   0
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

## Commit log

2019-07-12 July 12th Notes
    Highlights:
    * Replaced caster on Arlo.
    * Sticking with LPC1768 for now.
    * Want to try using BLE instead of WiFi for remote
    debugging/programming.
    * Figured out drive mechanics for rover.
    * Came up with part/tool list and ordered them. This includes a Prusa
    3D printer.
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2019-07-22 Fix UART error traps when LPC1768 not powered up
    When the LPC1768 isn't powered up, the nRF51 detects random transitions
    on its UART_RX_PIN input pin. This update switches on the pull-up for
    that pin to eliminate those random transitions.
    [main.c]
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2019-07-27 July 27th notes
    Highlights
    * Overview of additional BLEMRI updates.
    * Issues encounted with LewanSoul BusLinker board and LPC1768
    microcontroller.
    * IMU and OpenMV camera sensors ordered.
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2019-08-03 Enable deploying new binaries over BLE
    Commit includes:
    * A binary of my mriprog program from my
    https://github.com/adamgreen/bb-8 repository. This program can use
    blemri to program the LPC1768 wirelessly. I made a few fixes to this
    program based on issues I encountered and debugged while testing it
    with blemri.
    * Added a deployBLE script that uses mriprog to deploy the newly built
    LPC1768 binaries.
2019-08-03 Allow BLEMRI to handle more than GDB packets
    Previously the BLEMRI firmware running on the nRF51 expected GDB remote
    packets to be sent so it would buffer data until it was full or the end
    of a packet was received. This commit removes that limitation. Now it
    buffers up the data until the buffer is full or no UART data has been
    sent from the LPC1768 for 1.5 serial frames. This fixes an issue where
    it failed to send the GDB remote protocol ack ('+') for the continue
    command which resulted in GDB timing out and sending the continue
    command again. This would cause MRI to break into the running LPC1768.
    [main.c, sdk_config.h]
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2019-08-04 Add August 3rd Notes
    Highlights include:
    * I have 3D printed the LX-16A Servo Couplers.
    * Fixed a few bugs in BLEMRI that I encountred when I attempted to use
    it during the previous week's LX-16A Servo mbed driver work.
    * Explained how my mriprog program can use the MRI debug monitor to
    upload new code into a LPC1768 over a wireless serial connection.
2019-08-07 Add August 7th Notes
    Mostly discussing PETG stringing issue on wheels and how to correct it.
    I have decided not to commit .gcode files into this repository but the
    .3mf files instead. PrusaSlicer can be used to load these and generate
    the gcode as needed.
    [LX-16A - Coupler_5x.3mf, LX-16A - Coupler_Spare.3mf]
2019-08-10 Added August 9th Notes
    * Discuss other Sawppy parts I have managed to print this week.
    * Slicing parameters used for fixed knuckle print.
    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
    [Fixed Knuckle.3mf, Fixed Knuckle_Mirrored.3mf, LX-16A - Bracket_5x.3mf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]
2019-08-19 Initial LewanSoul LX-16A Serial Bus Servo driver
    * HalfDuplexSerial driver for the LPC1768 which can switch the Tx pin
    between being a UART peripheral output and a GPIO input when it needs
    to switch between transmitting and receiving. This allows the LX-16A
    servo signal wire to be connected to both the Tx and Rx pin of the
    LPC1768's UART. The driver takes care of making sure that the LPC1768
    doesn't drive the signal wire when the LX-16A is responding to a read
    request.
    * NOTE: In the future I might try to make the HalfDuplexSerial driver
    support async operations by taking advantage of DMA so that the
    CPU can be freed up for other important tasks o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
    [main.cpp]
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2019-10-06 October 5th, 2019 notes
    * Robothon 2019 competition was run today.
    * I have 3D printed more Sawppy parts.
    * Struck out previous note about not using Stealth mode on the Prusa i3
    MK3S to reduce PETG stringing but further testing shows that it
    doesn't have that big of an impact.
    * Added PrusaSlicer .3MF files for the parts that I have printed since
    the last update.
    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
    [Bogie-Body.3mf, Bogie-Body_Mirrored.3mf, Bogie-Wheels.3mf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]
2019-10-24 Add PrusaSlicer configs for latest parts
    * Differential parts
    * Body corners
    * 3mm nut clips
    [Body Corner.3mf, Clip2n125_50x.3mf, Clip3n20_20x.3mf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]
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2020-01-24 Create SawppyDrive class
    My initial attempt at abstracting the Sawppy driving code out into its
    own C++ class. I will probably pull the state machine used to
    transition from driving to/from turn in place modes into this class as
    well so that the calling code doesn't have to know about it. I am just
    not setup to properly test it now with the limited CLI that I currently
    have.
    This code is based on Roger Cheng's (@Roger-random) original Arduino
    sketch:
    https://github.com/Roger-random/Sawppy_Rover/blob/master/arduino_sawppy/arduino_sawppy.ino
    [main.cpp]
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2020-02-03 Initial commit of BleJoystick firmware
    This is a basic proof of concept firmware for the handheld joystick/
    deadman switch hardware to be used with the Power Distribution Board
    (PDB). It will be updated in the future as I get closer to final
    hardware.
    The current features/limitations include:
    * I currently have it running on a micro:bit that I had onhand. This
    meant that I had to hack the BSP stuff a bit since its button/LED
    layout differs a bit from the other boards supported by the SDK. It
    also needs to use the RC option for the low frequency clock since it
    doesn't have a crystal for that purpose. This board also has 16k less
    of RAM that the boards/modules that I typically use.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
    [main.c, sdk_config.h]
2020-02-04 Fixes to BleJoystick
    * Fix the Makefile so that "make flash" works by setting the nrfTool
    folder name correctly in this rule.
    * Perform the first battery voltage measurement soon after reset so
    that it doesn't need to wait for the first 1/2 minute timeout
    before making the first measurement. Previously it sent 0.0V over BLE
    for the first 1/2 minute after reset.
    [main.c]
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2020-05-25 Close relay when remote deadman switch pressed
    I connected the relay control input to P8 (P0.18) of the micro:bit and
    used it to close the motor power relay when the deadman switch was
    depressed on the remote BLE unit. The BJT controlled by this digital
    output requires a base current of 5mA so P8 was configured for high
    current drive. I also needed to modify the Sparkfun Beefcake Relay
    Control Board to replace the 1k base resistor with a 680 ohm unit so
    that enough CE current was allowed to flow through the relay when using
    a 3.3V digital output. Without this change, the relay wouldn't fully
    close when the BJT was turned on.
    I also commented out most of the LCD display test code as I wanted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
    [main.cpp]
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2020-05-25 Update blemri firmware
    I used the new C structure initializer format with named struct fields
    for setting up the UART connection parameters to make it easier to
    read. I had used this format in some of my newer nRF51 code so I
    backported it to this project too.
    I also fixed a bug in its Makefile to pull the programming tools from
    the correct folder. I had already fixed the other nrfjprog
    instantiations but missed the one for the "flash" rule.
    [main.c]
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2020-07-06 Version 1 of Power Distribution Board
    This is my first KiCAD project, the Power Distribution Board for my
    RoboMagellan bot. This version was sent off to OSHPark for
    manufacturing on July 5th, 2020.
    [PDB.kicad_pcb, PDB.sch]
2020-07-06 Sliced Sawppy battery tray files
    I might not end up using exactly the same tray for my battery but it
    will be similar so I printed off Roger's design so that I can get a
    better feel for what I would like to customize.
    [Battery Tray.3mf, Battery Tray_MIrrored.3mf, Power Panel.3mf]
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2020-07-06 Use correct template for PDB schematic
    I had moved my page layout description template to a different folder
    and forgot to update the schematic page layout to point to the new
    folder.
    [PDB.sch]
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2020-07-12 Update link for 470pF cap
    My existing book of 0805 caps doesn't have a 470pF ceramic capacitor so
    I updated the link to point to the one from Digikey that I have
    ordered.
2020-07-19 Add remote control mock-ups
    Adding openSCAD designs for the current mockup of what I am planning
    for the remote control. I worked on these at the same time as the PCB
    layout as the two are dependent on one another. This mockup is solid
    with no room for actual electronic or mechanical parts.
    [9032.STL, RemoteControlBottom.3mf, RemoteControlBottom.scad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]
2020-07-20 Version 1 of Remote Control
    This version was sent off to OSHPark for manufacturing on
    July 20th, 2020.
    [PDB.kicad_pcb, RemoteControl.kicad_pcb, RemoteControl.sch]
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2020-07-26 Update PDB firmware for new PCB
    Changes included:
    * Switching the pins used for the LCD, relay input, and UART from what
    was used with the micro:bit prototype and my custom designed PCBs.
    * I also moved the BSP input/output pins to ones that wouldn't conflict
    with anything actually being used by the nRF51 module.
    NOTE: I need to remove the BSP stuff completely from this code in the
    future as I don't have any LEDs or buttons dedicated to BSP
    functionality on this board.
    * I also updated NRF_CLOCK_LFCLKSRC to set it correctly for the nRF51
    module I am using.
    [main.cpp]
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2020-08-01 July 31st notes
    Getting much closer to being done with the PDB firmware and I added a
    few bodge wires to the PCB to fix mistakes in my initial version of
    the board.
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2020-08-04 ST7789 LCD driver cleanup
    There are some things that the ST7789 driver inherited from Adafruit
    precursors dealing with screen size and rotation that I don't like so
    I have modified this driver to correct them:
    * I don't like that a rotation of 0 actually asks the driver to invert
    the x and y axis when writing pixels while a rotation of 2 does no
    such inversions. Why isn't a rotation of 2, the default (0) rotation?
    Well in my version of the code, it now is.
    * The driver had constants for the screen dimensions and offsets. The
    driver should be specific to the driver chip and not the LCD to which
    it is attached. I modified the code to take the screen dimensions and
    offsets in the co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
    [Screen.cpp]
2020-08-04 Switch screen orientation back to correct value
    I also modified the code to still use hardware vertical scrolling when
    in orientation 0 and switch to software scrolling for any other
    orientation. I could probably flip the vertical scan direction and
    have it work in orientation 2 as well but I don't need that at this
    time.
    [Screen.cpp]
2020-08-04 Remove LCD libraries no longer being used
    Now that I have switched to @cbm80amiga's Arduino_ST7789_Fast library
    I no longer need these Adafruit ones.
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2020-08-04 RREFont updates
    Most of the changes were to just get it to build for nRF51. I did
    switch from a callback for the fillRect function and used an interface
    instead so that I didn't need a global function. I added this interface
    to the Arduino_SST7789 class. I also used const char* pointers instead
    of char* pointer where possible.
2020-08-04 Improve LCD performance
    I decided to restore cbm80amiga's NOP method of making sure that the
    last byte has been sent out over SPI before sending the next byte or
    changing the state of the CS or DC pins. This got me a 3x performance
    improvement over my checking of the READY event. The software text
    scrolling looks pretty good now.
    I can issue 100 clear screens in 12 seconds for ~7,680,733 bps.
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2020-08-05 Update remote control firmware for new PCB
    Updated firmware to work on the new PCB once I had it soldered up and
    ready for testing:
    * Switched to the new pin mappings.
    * Made sure that unused BSP pins didn't conflict with pins being used
    for other things on the module. I would like to remove the BSP code
    altogether in a future commit as I shouldn't really need it. Removed
    UART pin definitions since my code doesn't use the UART.
    * Now provide power to joystick pots via a nRF51 pin so that it can be
    turned off when sleeping to reduce power usage.
    * Switched the low frequency clock sources to be appropriate for the
    nRF51 module.
    [main.c]
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2020-08-05 PDB firmware fixes
    * Now set CS_ALWAYS_LOW to 1 or 0 to enable/disable the feature instead
    of defining to enable and not defining to disable. This allows normal
    conditionals to be used within code instead of littering it with even
    more #ifdefs.
    * Removed some more commented out code in Screen.cpp
    * Updated Screen::update() to make a local copy of PdbState before
    making use of it so that everything in the function sees a consistent
    view of the state. Before it was possible that a BLE interrupt would
    fire in the middle of the function and modify parts of the state
    which had already been written to the screen. This means that it
    could fail to remember what changes it just made t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
    [Screen.cpp]
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2020-08-09 Flip X/Y pots in remote control firmware
    [main.c]
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2020-08-09 Faster detection of BLE remote control disconnect
    The BLE central device doesn't consider a BLE peripheral to be
    disconnected for a few seconds after it stops seeing radio traffic from
    the device. This improves robustness to short bursts of radio
    interference but in our case, we want the motors to be disabled as soon
    as the radio connection is broken. Otherwise it might miss us releasing
    the deadman switch if there was radio interference at the same time.
    I refactored the code to have the LCD update timer code check to see if
    the BLE stack has received new packets since its previous iteration. If
    it doesn't see any BLE traffic for 2 iterations of the LCD timer then
    it considers the remote t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
    [Screen.cpp, main.cpp]
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2020-08-10 Add watchdog timer
    If the lcdTimeoutHandler() timer routine doesn't run in 250 msec to
    feed the watchdog then the PDB will reset. I have configured the
    watchdog to pause when halted in the debugger.
    [main.cpp, sdk_config.h]
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2020-08-13 Update mriprog binary
    New mriprog contains a fix to properly halt the code running on the
    LPC1768 before uploading the bootloader. Before it only worked if the
    code was already halted when mriprog attached.
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2020-08-18 Move CAD files into separate files
    PDB files are now in cad/PDB and remote control ones are now in
    cad/RemoteControl.
    [9032.STL, PDB.3mf, PDB.scad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]
2020-08-21 Update PCB with joystick
    * Replaced Sparkfun's 9032.STL representation of the joystick with the
    Sparkfun_9032.scad design that I created myself from measurements of
    the joystick.
    * Updated PCB representation to more closely match the actual PCB by
    adding rounded corners, mounting holes, and right angled deadman
    switch.
    [9032.STL, RemoteControlTop.scad, Sparkfun_9032.scad]
2020-08-22 August 21st notes
    Show some photos of my current remote control enclosure progress.
    [RemoteControlTop.scad]
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2020-08-30 Fix bumper thickness
    Had parameter to set it but I was hardcoding it to 1.0mm in
    ButtonBumper() module.
    [Button.stl, Common.scad]
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2020-09-05 Add all.scad
    This OpenSCAD sourcefile renders all parts of the remote control and
    animates them in and out of their correct position.
    I also did some minor cleanup in Common.scad
    [Common.scad, all.scad]
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2020-09-27 Update PDB back panel design
    It no longer slides in but has a single M3 screw that holds a plate
    inplace.
    [Common.scad, Door.stl, PDB.3mf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]
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2021-04-11 April 11th notes
    I swapped out the green manual/auto switch for a red version.
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2021-04-21 Copying over orientation app from Ferdinand16
    This is the Processing application I wrote back in 2016 to show the
    orientation of the IMU sensor. It supports multiple modes of
    calculating this orientation:
    * Accelerometer/Magnetometer data only. This is noisy and doesn't work
    well when the IMU itself is being accelerated due to robot motion.
    * Gyro rates only. The rotation rate integration used by this method
    results in error accumulation. In the short term, it provides very
    smooth orientation results but drifts in the long term. It can
    also only detect relative changes in orientation and not absolute
    orientation like the accelerometer/magnetometer combo.
    * Kalman filter running on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
    [ConfigFile.pde, HeadingSensor.pde]
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2021-04-22 Sample sensors on FXOS8700CG data ready interrupt
    Previously I was using a 100Hz timer but the FXOS8700CG errata
    indicates that it is better to sample right after data is ready to
    reduce I2C traffic while magnetometer is being sampled.
    [main.cpp]
2021-04-22 Sample rate now in config.ini
    Can now set the sample rate in config.ini rather than be hardcoded in
    the Java and C++ source code. 200Hz seems to work ok but 400Hz turns
    out to be too fast for the UART to keep up when sending the full larger
    packets. Would work on the robot itself though since it wouldn't need
    to send the data out over the UART.
    NOTE: I also updated the compass.gyro.scale in config.ini to just be
    the 16.0 value from the datasheet instead of my badly measured
    values.
    [ConfigFile.pde, HeadingSensor.pde, config.ini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]
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2021-05-19 Add virtual encoders and PID control to LX-16A servos
    This commit includes:
    * A simple program in the software/EncoderTest to test forward and
    reverse closed loop operation of the servos.
    * Copied over my PID library from the Ferdinand16 repository and made a
    few updates:
    * Now allow the sample time to be updated for each iteration and not
    just fixed at construction time.
    * The constructor now takes a function pointer for a
    pErrorConstrainCallback that can be used to constrain the error
    (ie. constraining an angle error to be between +/-180 degrees) used
    for the PID calculation.
    * I added a few more constants to LX16A.h as a convenience to code
    making use of this lib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
    [main.cpp]
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2021-05-31 Update blemri to work on newer macOS
    I hit 2 issues on my newer MacBook Air running Big Sur:
    * Once the Mac has been connected to a BLE device such as BLEMRI, macOS
    only returns the information that it cached on the first connection
    and this doesn't include the 128-bit service UUID from the scan
    response. My code used this UUID for filtering when performing BLE
    device discovery. I modified the firmware to no longer advertise the
    unique service UUID and now just advertise the Nordic UART service
    UUID actually supported by the device as it is no longer of use for
    filtering. I now have the application running on macOS perform BLE
    discovery with no filtering and then check the lo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
    [main.c]
2021-06-01 Increased BLE interval in BLEMRI firmware
    I increased the minimum and maximum connection interval from 7.5ms to
    15ms to meet the Apple design recommendations. My iPhone is now able to
    stay connected for over 100 seconds.
    This change doesn't decrease the throughput that much as BLE allows
    multiple packets to be scheduled per interval. It would increase the
    turn around time to get the response back from commands. The throughput
    is still above 5kB/s after this change so I will keep it.
    I also added comments to document Apple's recommendations for these
    various connection parameters.
    [main.c]
2021-06-05 LX-16A servo driver cleanup
    Changes include:
    * Fix text in LX16A_Servo::getPosition() read error message.
    * Don't perform a full reset in LX16A_DriveMotor from constructor as
    it requires communication with the servo which might not be powered
    at init if Dead Man switch isn't pressed by the user. The application
    code can kick off the full reset when it sees the motor power
    re-enabled.
    * Deleted some commented out code in LX16A_DriveMotor::getPower().
    * Removed some debugging printf() calls from LX16A_DriveMotor.
2021-06-05 SawppyDrive now uses closed loop control for LX-16A servos
    * Now use LX16A_DriverMotor instead of LX16A_Servo for the 6 rolling
    servos controlled by the SawppyDrive class. These add the closed loop
    control for rotational speed.
    * Instead of using open loop power settings for controlling the 6
    drive servos, the percentage speed settings are used to set the
    desired rotational speed in rad/s where the maximum velocity of
    3.0 rad/s is used when the speed value is set to 100.
    * Added void SawppyDrive::reset() method to call reset() method on all
    6 of the drive servos to initialize the PID and state estimates when
    the servos are powered back up.
    * I updated the Sawpp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
2021-06-07 Improve blemri throughput back to PC
    The code now queue up as many of the chunks directly to the BLE stack
    until it gets a BLE_ERROR_NO_TX_PACKETS error. Once that error is
    received, the packets are placed in the chunk queue which drains as the
    BLE stack completes the sending of previous chunks. Once this queue is
    drained, the code will go back to submitting directly to the BLE stack
    again.
    I can now successfully use the DebugSerial class to send debug spew
    back to GDB and GDB feels much more responsive after I made this
    change since it lets the BLE stack know that it can transmit more
    than 1 chunk per connection interval.
    [main.c]
2021-06-09 Improve LX16A servo error handling
    Sometimes the LX16A servos will fail to return the current angle
    reading:
    * If I am spamming the half-duplex serial bus a little bit too often.
    * If the motors were just powered down via my deadman switch.
    This commit includes a few changes to more gracefully handle such
    failures:
    * The HalfDuplexSerial driver now detects line errors that can occur
    when the motors are powered down in the middle of a read request:
    framing error and break interrupt. When these errors are detected,
    they are flagged in HalfDuplexSerial::verifyNoErrors() and
    HalfDuplexSerial::read() will still read as many bytes as possible
    off of the serial line but return a bytes re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
2021-06-09 Move include/ and libs/ back into software/
    That way they are all covered by the same LICENSE.TXT in software/. I
    also placed a copy of LICENSE.TXT in the processing/ folder as well.
    I also moved EncoderTest into libs/LX16A since it is a test for that
    library and I probably won't revisit it a lot in the future.
    [main.c, main.cpp]
2021-06-28 Split IMU reading code to SPI slave
    My main LPC1768 microcontroller doesn't have any I2C capable pins
    available but it does have one set of SPI pins still free. This commit
    includes the ImuSlave firmware which turns a nRF52 board into a SPI
    slave which reads the IMU sensors via I2C and then sends the
    measurements to the main LPC1768 over SPI.
    * AdafruitPrecision9DoF constructor now takes the sampling rate as a
    separate parameter so the nRF52 sensor reading only code can pass in
    NULL for the pCalibration parameter but still provide the required
    sampling rate. I updated the Heading sample to work with this change
    as well.
    * I copied a bunch of the AdafruitPrecision9Do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
    [FXAS21002C.cpp, FXOS8700CQ.cpp]
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

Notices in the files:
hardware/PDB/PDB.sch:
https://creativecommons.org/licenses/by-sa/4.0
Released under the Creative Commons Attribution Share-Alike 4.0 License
